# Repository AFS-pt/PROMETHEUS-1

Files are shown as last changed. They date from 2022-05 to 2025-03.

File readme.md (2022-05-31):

# PROMETHEUS - PocketQube Framework Designed for Research and Educational Access to Space

## Project Summary

The PROMETHEUS project aims at providing easy access to space for the research and education (R&E) community. Learning or researching about space can be more fruitful via hands-on projects. However, Space can seem like a pitfall environment with high risks and therefore high costs to develop projects at the student level. This barrier is critical and hinders R&E opportunities given the lack of experience in this environment. The team has identified that there is no current tool that enables easy and low-cost access to such space experiences of learning or manufacturing a simple satellite device. Looking into [Portugal’s Space 2030 national strategy](https://ptspace.pt/space-2030/), where we witnessed the creation of the [Portuguese Space Agency](https://ptspace.pt) and other related entities, the growing educational programs offered in Aerospace Engineering and the increasing interest of young students and researchers in this field, there is here an opportunity and a need to provide key tools to generate human critical mass.

The PROMETHEUS project aims at being a contributor for this momentum, by serving as an open-source PocketQube platform.

A PocketQube is a small satellite in a 5 cm cube form factor, an ideal size for R&E. The platform here proposed is based on the [PyCubed](https://github.com/pycubed) system (an open-source, radiation tested CubeSat avionics platform that integrates power, computing, communication, and attitude determination and control functionality into a single low-cost PC104-compatible module programmable entirely in Python), previously developed by the CMU team. This means that the entire system is widely available, based on commercial-off-the-shelf components and open-source hardware and software. From the foundation, the proposed platform has all the minimum required conditions to be easily integrated as a tool that facilitates hands-on activities and access to space.
But the PROMETHEUS goes beyond that and shares the entire pipeline for the satellite deployment as it will be licensed, certified, and launched. These steps are critical as, although there are a few design frameworks for PocketQubes available, there is a lack of information about the suitability of such designs to sustain the launch process. Moreover, from the licensing process, and considering that it needs to be performed through the competent national authorities, best-practice guidelines documentation is lacking among the community and if one intends to provide such a tool, it is important to share experiences and hurdles in this process.

**PROMETHEUS aims at giving access to space for everyone.**

## Expected Outputs

PROMETHEUS’s main objective is to provide a PocketQube platform that is tested and validated in space, and to make it openly available for everyone to replicate and customize. To accomplish such a goal, the following milestones/outputs need to be reached:

1. Tune the PyCubed platform for the ProcketQube form factor (PROMETHEUS blueprints).
2. Build the PROMETHEUS in different locations and by different people, based on the provided blueprints (replication validation).
3. License and certify the PROMETHEUS (authorization documentation).
4. Launch and validate
5. Share the knowledge (disseminate PROMETHEUS)

If all milestones are successfully accomplished, PROMETHEUS will be the first Portuguese PocketQube in space, as a result of a joint endeavour between Portuguese and CMU researchers, and hopefully will open the road for other national and international groups to do the same.

## Acknowledgment

The project "PROMETHEUS - PocketQube Framework Designed for Research and Educational Access to Space" (ref. CMU/TIC/0017/2021) is supported by [Portuguese Foundation for Science and Technology](https://www.fct.pt/index.phtml.en) under the International Partnership [CMU Portugal Program](https://www.cmuportugal.org), in a consortium between [Universidade do Minho](https://www.uminho.pt/EN/Pages/default.aspx) (PT), [Instituto Superior Técnico](https://tecnico.ulisboa.pt/en/) (PT) and [Carnegie Mellon University](https://www.cmu.edu) (USA).

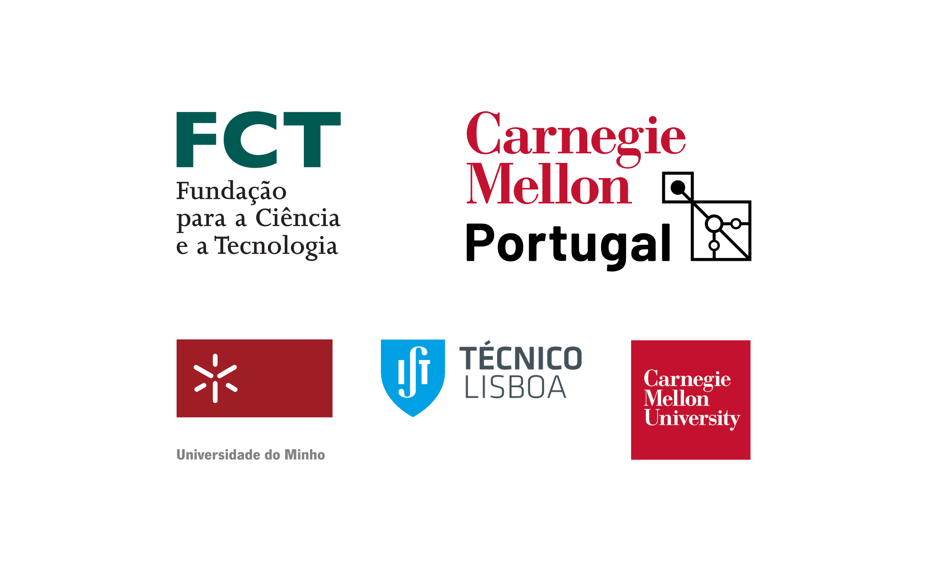
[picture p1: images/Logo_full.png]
My Image


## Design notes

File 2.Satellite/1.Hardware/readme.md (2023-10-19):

# Boards

2023-02-03 - forked from PyCubed-Mini

# Mechanical Structure

2023-02-03 - forked from PyCubed-Mini

3D-printed structural material: Windform XT2

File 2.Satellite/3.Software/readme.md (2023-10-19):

# Software Testing

## Description

The mainboard (red) has all the main components present in the satellite, such as the microcontroller (ATSAMD51J19A), LoRa chip (RFM98), as well as some power and data management. The Z- Board (blue) is one of the edges of the PocketQube, designed to interface four solarpanels and the antenna.

RExLab Team shared some useful [documentation](https://pocketqube.readthedocs.io/en/latest/index.html) about the uC software implementation and a detailed CAD model of the satellite. Nevertheless, their Github repos contain most of the important info and code (https://github.com/PyCubed-Mini: /fight_software, /avionics-..., /Tests).

The uC is programmed in CircuitPython, which can be coded using Mu Editor. The code that arrived inside the board is inside "Software on board" folder.

<p align="middle">
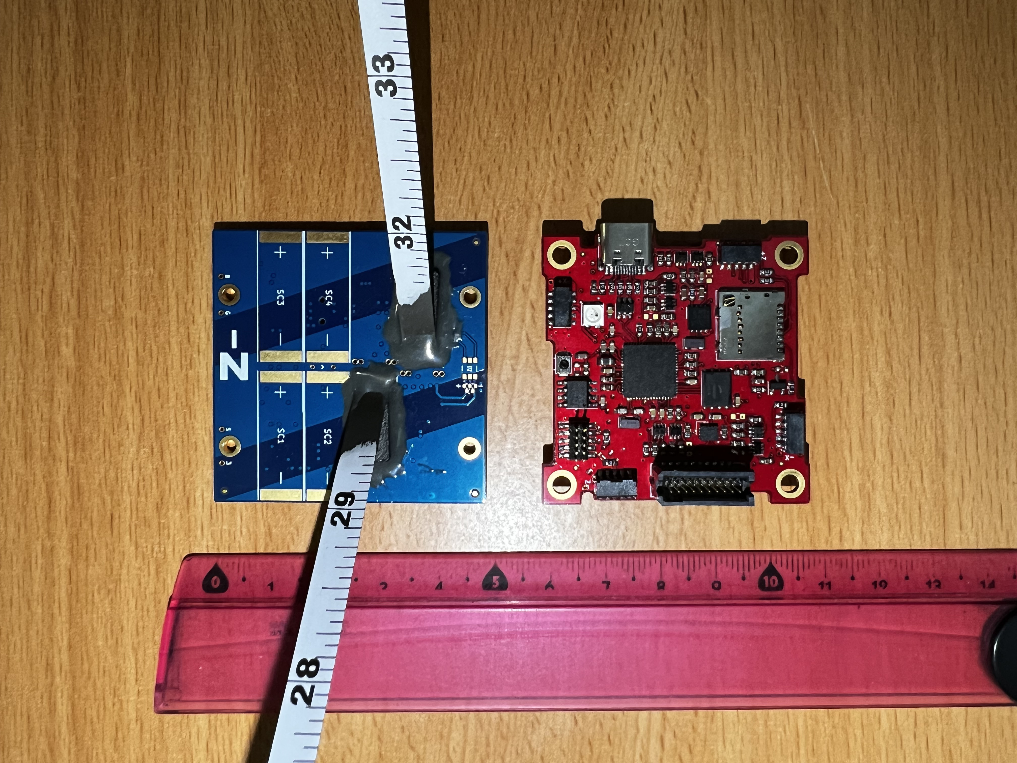
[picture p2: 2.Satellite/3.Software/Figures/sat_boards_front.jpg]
  
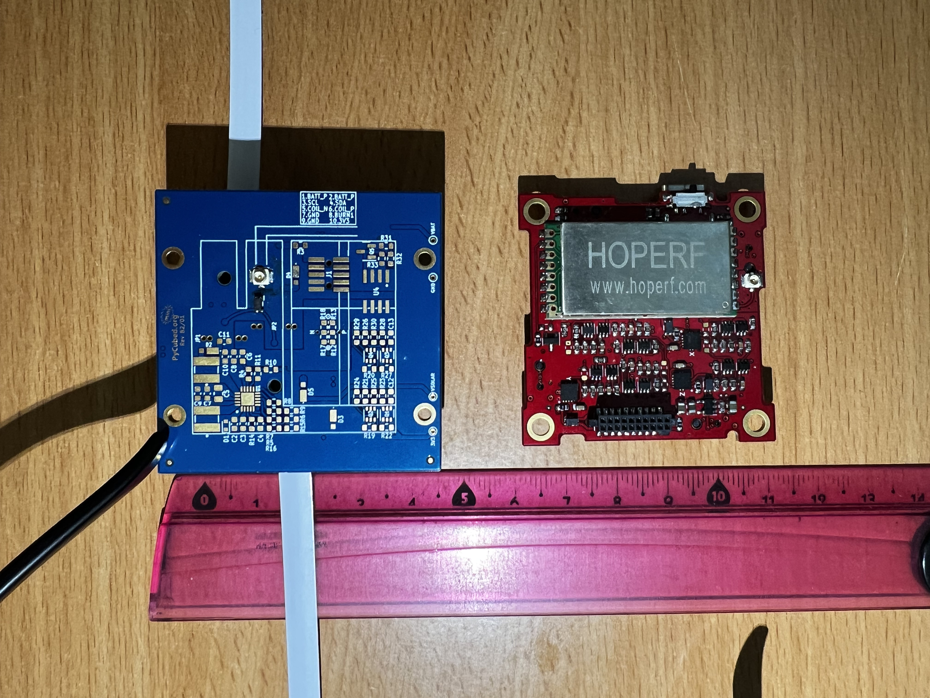
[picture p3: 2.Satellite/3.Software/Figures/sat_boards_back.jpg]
  
</p>

<br>

## First steps

1. Install Mu Editor from [Adafruit website](https://learn.adafruit.com/welcome-to-circuitpython/installing-mu-editor);

2. Connect an USB cable between your computer and the board;

3. Make sure that the switch below board USB-C port in turned on (right position);

4. Double-tap the button (there is only one);

5. If a USB unit isn't detected, there might be two issues:
    - Double-tap timing is wrong (keep trying);
	- USB-C connection (flip the USB-C cable at board connector);

6. Paste the code and libraries you want to run on the uC inside the USB unit;
    - See below the code used for testing LoRa packets transmission from satellite board to ground station [LILYGO® TTGO T-Beam v1.1](https://meshtastic.org/docs/hardware/devices/tbeam/);
    
7. In Mu Editor, open file from folder (main.py, for example) and open Serial Viewer;

8. Saving file edits should recompile the program, execute your code and show prints in serial data. If not, try Ctrl+D in Serial Viewer;

<br>

## Transmission from satellite board to ground station (LILYGO® TTGO T-Beam v1.1)

First, the steps needed for the ground station (receiver):

1. Install Arduino IDE;

2. Install the ESP32 board drivers (follow this [tutorial](https://randomnerdtutorials.com/installing-the-esp32-board-in-arduino-ide-windows-instructions/));
    - In our case, the board reference changes to 'TTGO LoRa32-OLED' and the COM port may be defined to another instance;

3. Install the libraries needed for peripherals, such as the OLED and LoRa chip (follow this [tutorial](https://randomnerdtutorials.com/ttgo-lora32-sx1276-arduino-ide/));

4. Create a project with the sender sketch from the last tutorial, compile, run and open Serial Viewer, configured with the correct parameters;
    - Again, in our case, change the board pins (MISO, SDA, ...) to the correct ones and frequency (433MHz);

5. The OLED should display the init prompt and starting to send packets;

Then, the steps needed for the mainboard (transmitter):

6. Download the Tests repo from PyCubed-Mini, more specifically the [LoRa Radio Range Test](https://github.com/PyCubed-Mini/Tests/tree/main/lora_radio_range_test) and do step 6 from last chapter;
    - This repo is really helpful since it has implemented easy and reliable testing routines to major components, such as the LoRa chip;
    - In our case, some modifications were necessary, such as the node address, receiving settings and string printing;

7. In the Seriel Viewer, it should prompt a interactive menu of the testing routine;

8. Select the satellite option, following the radio parameters change;
    - In our case, the default options were fine;

9. Finally, you should set the receiving mode with acknowledge;

10. In a few seconds, it should print the received LoRa packet info, such as the RSSI and the message;
    - As it is, the first four chars are not being printed as we hoped so;

<p align="middle">
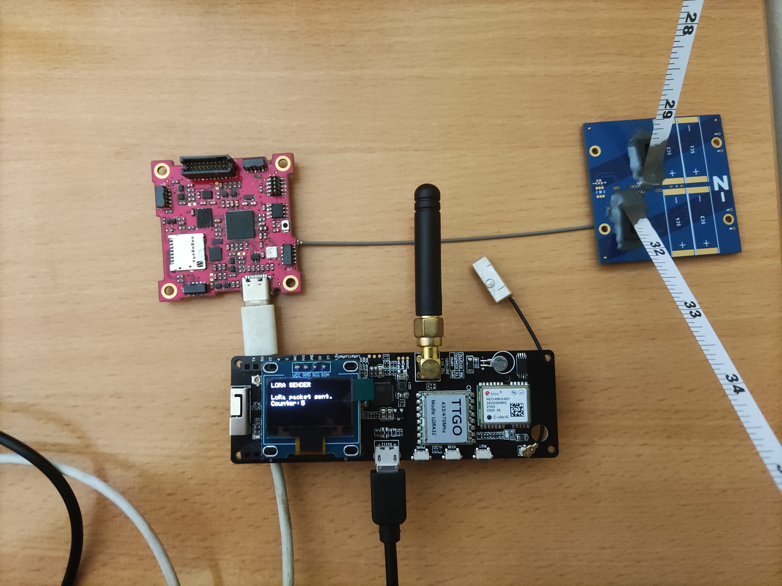
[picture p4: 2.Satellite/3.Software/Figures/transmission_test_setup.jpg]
  
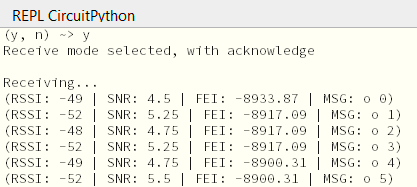
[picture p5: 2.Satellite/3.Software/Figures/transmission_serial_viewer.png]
  
</p>

<br>

## Transmission from ground station to satellite board

Not started but should be similar, since the satellite transmitting code could be functional in our case and the ground station receiving code could be like the one showed in the previous mentioned tutorial.

<br>

## Credits

We shared our files used, with our needed changes implemented, however we give all the credits to the rightful creators.

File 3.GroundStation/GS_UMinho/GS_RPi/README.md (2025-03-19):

# Raspberry Pi Ground Station

A small modular radio to chat with satellites.

## Features

- LoRa UHF communication (TX and RX);
- Compatible with Raspberry Pi (40-pin header);
- Programmed with CircuitPython;
- Independent power supply to increase performance;
- Dedicated to PROMETHEUS-1 satellite.

For more details on the RFM98 radio module, check the [short](https://www.hoperf.com/uploads/RFM98PW_RFM95PWRFTransmitterandReceiverModuleDatasheetREV1.1_1695351516.pdf) and [detailed](https://cdn.sparkfun.com/assets/learn_tutorials/8/0/4/RFM95_96_97_98W.pdf) datasheets.

## Hardware

### Issues

A few issues from RPiGS v2 were discovered during testing, which could be fixed in a new iteration (v2.1). These issues are detailed below:

1. [RESET pin of RFM9x radio should not have a pull-up resistor](https://github.com/adafruit/Adafruit_CircuitPython_RFM9x/pull/47):
    - v2: Resistor is present on both, but do not phisically assemble it.
    - v2.1: Resistor should be removed;

2. [Raspberry Pi pins CE0 and CE1 should not be used for GPIO purposes](https://learn.adafruit.com/circuitpython-on-raspberrypi-linux/spi-sensors-devices):
    - v2: CS pin is connected to CE0, but this line can be rearranged to another pin (such as D6) via software.
    - v2.1: RESET and CS pins from radio should be rerouted to other free GPIO pins;

3. Hat board power supply cannot power Raspberry Pi startup due to high initial current:
    - v2: radio and Raspberry can be powered by either Raspberry power module or by external power source.
    - v2.1: Raspberry should be only powered by its own power module, radio could be powered by either Raspberry power module or by external power source (probably increase transmission power).

## Software

### Instructions

#### Dependencies

Before using the RPiGS, make sure you have all the requirements, such as SPI enabled and CircuitPython installed. 

Based on [Adafruit tutorial](https://learn.adafruit.com/circuitpython-on-raspberrypi-linux/installing-circuitpython-on-raspberry-pi):

> Run these commands to enable the various interfaces such as I2C and SPI:
> ```bash
> user@machine ~
> $ sudo raspi-config nonint do_i2c 0
> $ sudo raspi-config nonint do_spi 0
> $ sudo raspi-config nonint do_serial_hw 0
> $ sudo raspi-config nonint do_ssh 0
> $ sudo raspi-config nonint do_camera 0
> $ sudo raspi-config nonint disable_raspi_config_at_boot 0
> ```
> 
> Then, install Blinka package and its dependencies with:
> ```bash
> user@machine ~
> $ sudo apt-get install -y i2c-tools libgpiod-dev python3-libgpiod
> $ sudo pip3 install --upgrade adafruit-blinka
> ```

Note that `--break-system-dependencies` might be needed. If it is undesirable please visit the original tutorial and install the package with a virtual environment.

> In Raspberry Pi model 5, RPi.GPIO is installed which causes issues. Just remove it with the following command:
> ```bash
> user@machine ~
> $ sudo pip3 uninstall -y RPi.GPIO
> ```
> 
> This script will automatically enable I2C and SPI. You can run the following command to verify:
> ```bash
> user@machine ~
> $ ls /dev/i2c* /dev/spi*
> ```
> 
> You should see the response:
> ```bash
> /dev/i2c-1 /dev/spidev0.0 /dev/spidev0.1
> ```

The following commands should also be executed if the hardware version is v2, as described in the issue #2 above.

> CE0 and CE1 can be reassigned via software with the commands:
> ```bash
> user@machine ~
> $ cd ~
> $ sudo pip3 install --upgrade adafruit-python-shell click
> $ wget https://raw.githubusercontent.com/adafruit/Raspberry-Pi-Installer-Scripts/main/raspi-spi-reassign.py
> $ sudo -E env PATH=$PATH python3 raspi-spi-reassign.py --ce0=5 --ce1=6
> ```
> 
> After this, the package should be properly installed. You can verify it with the following code:
> 
> ```python
> import board
> import digitalio
> import busio
> 
> print("Hello, blinka!")
> 
> # Try to create a Digital input
> pin = digitalio.DigitalInOut(board.D4)
> print("Digital IO ok!")
> 
> # Try to create an I2C device
> i2c = busio.I2C(board.SCL, board.SDA)
> print("I2C ok!")
> 
> # Try to create an SPI device
> spi = busio.SPI(board.SCLK, board.MOSI, board.MISO)
> print("SPI ok!")
> 
> print("done!")
> ```

#### Code

To run the ground station software, use the following command:
```bash
user@machine ~/PROMETHEUS-1/3.GroundStation/GS_UMinho/GS_RPi/Software/
$ python gs_shell.py
```

After this a prompt menu should appear, where you should select the option below to work with RPi_GS v2.
```bash
(o) RPiGS TX and RX (single radio)
```

Next, you can modify the radio parameters via prompt, but mind that these are the defined settings for PROMETHEUS-1. 

After this, you'll reach the ground station menu where you can request beacons, images, send commands, etc.

### References

Check the repositories from this was forked from:

- RPiGS single modem HW: https://github.com/cmu-spacecraft-design-build-fly-2023/Ops-Groundstation
- RPiGS dual modem HW: https://github.com/PyCubed-Mini/RPIGS/tree/main/rpi_dual_rfm98_hat
- RPiGS TX+RX LoRa/FSK SW: https://github.com/PyCubed-Mini/basic_groundstation/tree/image_radio_modes

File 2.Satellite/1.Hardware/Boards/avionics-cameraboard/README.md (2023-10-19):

avionics-cameraboard
Version B3/02
for updated versions, please consult https://github.com/PyCubed-Mini/avionics-cameraboard

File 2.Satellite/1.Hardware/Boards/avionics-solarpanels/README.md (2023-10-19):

# Solar Panels
PyCubedMini Solar Panel KiCAD projects.
Version B3/02
for updated versions, please consult https://github.com/PyCubed-Mini/avionics-solarpanels

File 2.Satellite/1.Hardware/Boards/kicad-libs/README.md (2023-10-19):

# kicad-libs
KiCad libraries for REx Lab avionics

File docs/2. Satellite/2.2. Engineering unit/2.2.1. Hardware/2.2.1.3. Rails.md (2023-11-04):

# Rails

Rails are the structural supports of the stack. There are two pieces in each stack, on the top and on the bottom, in which they hold inserts, sorted by the 3 axis. They provide the screwthreads needed for securing each external panels, as well as the upper and lower internal ones.

They are usually build from 3D-printed polylactic acid (PLA), since it is a cheap, simple and effective solution for granting the required rigidity for a testing unit.

Also made from PLA, two small brackets are needed for adjusting the antenna strips angle, holded in place with two M2 screws and nuts of nylon.

The 3D models of each rail and brackets are released in [Mechanical Structure](https://github.com/AFS-pt/PROMETHEUS-1/blob/main/2.Satellite/1.Hardware/Mechanical_Structure).

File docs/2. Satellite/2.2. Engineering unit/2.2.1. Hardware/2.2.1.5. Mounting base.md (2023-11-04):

# Mounting base

The mounting base is 3D-printed from PLA to provide a stable and safe piece to the satellite be placed on. Also it helps to place it on a flat surface and to hold it without pressing any components. The sliding required to insert the satellite facilitates the trigger of the switch mechanism stated previously.

The 3D model is released in [Fixtures](https://github.com/AFS-pt/PROMETHEUS-1/blob/main/2.Satellite/1.Hardware/Fixtures).

Mounted satellite

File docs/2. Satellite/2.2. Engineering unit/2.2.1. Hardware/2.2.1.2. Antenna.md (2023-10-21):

# Antenna

When simplicity and flexibility are two major parameters when designing an foldable antenna for this satellite, conductive tape measure comes in hand to develop a feasible solution.

<br />

## Antenna strips

As mentioned before, the satellite antenna, composed of two tape measure strips, is soldered to the defined Z- board pads. The metallic tape measure required for the process must be of approximately 1 cm in width, be almost planar and if possible, made of a easy-soldable material. The tape reference used for the assembly was DEXTER 8MM.

<br />

## Fishing line

The fishing line used for passing through the tape measure strip hole and the burn wire must be multithreaded, as each thread is smaller, they are melted easier when current passes through the burn wire. The line reference used for the assembly was CAPERLAM 4X 0.16 mm.

<br />

## Burn wire

The burn wire is made of nickel and chrome alloy of size AWG30.

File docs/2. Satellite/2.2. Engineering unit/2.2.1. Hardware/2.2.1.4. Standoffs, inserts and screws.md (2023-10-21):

# Standoffs, inserts and screws

There are three major types of mechanical parts required for the satellite, mentioned in the subtitle. They are recommended to be made of brass, since it has low density, or alluminum alternatively for the same reason.

<br /> 

## Standoffs

First, the standoffs separate each inside board with the adequate space between them. There were two sizes used: 6 mm and 4 mm in length, with eight M3 units needed for each size.

<br /> 

## Heat inserts

Then, the heat inserts, as referred before, provide the screwthreads needed for securing the external boards to the internal stack. There are needed 24 units in total: 4 units of M3, for attaching the -Y board to the stack; and 20 units of M2, for attaching X, +Y and Z boards.

<br /> 

## Screws

Finally, the screws fix the boards mentioned above, therefore, it is needed: 4 units of M3 (4 mm) for screwing -Y board to the -Y rail; 4 units of M3 (6 mm) screws for +Y rail to the stack; and 20 units of M2 (5 mm) screws for X, +Y and Z boards.

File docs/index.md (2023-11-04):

# Welcome to the PROMETHEUS-1 project wiki!

This website is composed of indexed pages which describe some important documentation about the satellite, such as its assembly. Please check the side bar for all available pages.

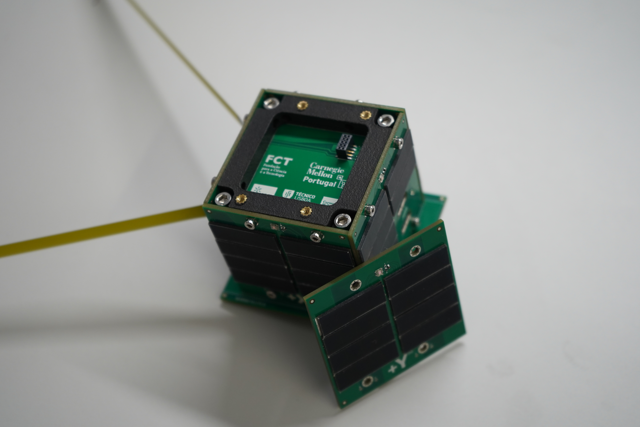
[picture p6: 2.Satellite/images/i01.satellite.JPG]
Satellite


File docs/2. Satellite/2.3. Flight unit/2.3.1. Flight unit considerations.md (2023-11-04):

# Flight unit considerations

This chapter explains only the different steps and precautions required during the flight unit manufacture, assembly and testing.

## Vibration testing and bake-out process

After the assembly, the satellite hardware must pass through vibration testing to certify that it can handle the launch. The vibration profile to test for is usually given by the launcher company and is specific for form factors or weight and the type of vibration. While all the tests are required for certification, usually the most important vibration test is the sinusoidal with frequencies up to 100 Hz, due to the predominance on launch. Consulting SpaceX Rideshare Payload User's Guide, the structure should handle at least 1.5 g. 

A vibe fixture was developed to couple the satellite with the vibration table, released on [Fixtures](https://github.com/AFS-pt/PROMETHEUS-1/blob/main/2.Satellite/1.Hardware/Fixtures). It is not recommended to use 3D-printed PLA as tends to damp higher frequencies and instead, consider alluminum for the case.

At last, the satellite goes through a bake-out process to accelerate outgassing, thus preventing contamination of the launcher pod and payload.

<br /> 

## Day in the life testing

Another important test is made to evaluate long-period satellite functioning. The test is performed by leaving the satellite running outdoors for an entire day, if possible being hit by the sun, to charge with the solar cells, and protected by the rain, to prevent damage. By the end of the test, the satellite should be running as it was left, and the batteries voltage be higher than previously.

<br /> 

## Assembly precautions

Before the procedure, drop and scrub the boards and its components with isopropyl alcohol (IPA). In this assembly procedure, more than required in engineering satellite units, the use of nitrile gloves and anti-static mat and wrist strap is very important. Although it is not mandatory, the assembly should be made in an ISO cleanliness certified room, if possible. Also, satellite transportation should be made inside an EMF protection bag, in a Nanuk case.

<br /> 

## Loctite usage

On flight unit, Loctite 222 is used in all screw surfaces. Just a few drops are enough to provide additional strength and prevent unscrewing.

<br /> 

## Windform rails

Instead of PLA rails, a carbon-fiber-reinforced polyamide material called [Windform XT 2.0](https://www.windform.com/sls-materials/windform-xt-2-0/) was used for the rails. It provides improved specific strength and NASA outgassing certification.

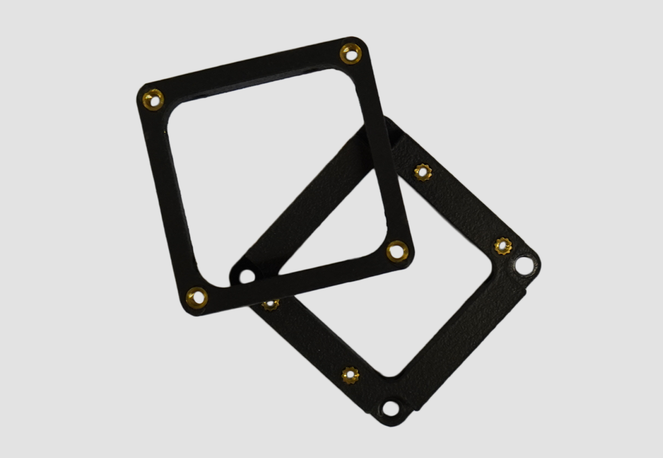
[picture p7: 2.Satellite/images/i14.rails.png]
Rails


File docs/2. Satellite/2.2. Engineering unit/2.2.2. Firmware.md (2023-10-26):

## Firmware

Preferably, you should skip building both the SAMD UF2 bootloader and CircuitPython files, as they are already released on [Firmware](/2.Satellite/Firmware), and skip to [Flashing SAMD UF2 bootloader](#flashing-samd-uf2-bootloader). However, some important references are given if you want to learn the required steps to build the [SAMD UF2 bootloader](https://github.com/PyCubed-Mini/uf2-samdx1) or [CircuitPython](https://github.com/PyCubed-Mini/circuitpython) yourself.

<br />

### Flash SAMD UF2 bootloader on mainboard

Based on [RExLab tutorial](https://github.com/PyCubed-Mini/avionics-mainboard/wiki/Flashing-UF2-Bootloader-on-the-ATSAMD51):

> The following procedure needs to be performed only once (barring any bricking / updating the bootloader) on a newly assembled mainboard with an unprogrammed MCU - in our case, the ATSAMD51J19A.
>
> <br /> 
>
> #### What you need
>
> - ATSAMD51 board (such as the PyCubed-Mini mainboard);
> 
> - Windows PC with atleast 2 free USB ports;
> 
> - SEGGER J-Link (we use the EDU Mini model);
> 
> - 2x5 pin 1.27mm pitch ribbon cable;
> 
> - USB-C and micro-USB cables, both with power and data lines;
>
> - SAMD bootloader binary file.
>
> <br /> 
>
> #### Step 1: Set up your PC
> 
> - Visit [Microchip Studio download page](https://www.microchip.com/en-us/tools-resources/develop/microchip-studio#Downloads), scroll down, and download the Web installer version of Microchip Studio. (The offline installer should also work, however I have had issues with antivirus software blocking it);
> 
> - Accept the Terms and Conditions, and deselect the "Send anonymous data" box. On the next page, select the architectures you'd like to install - we will only be using SAM boards. Finally, deselect "Advanced Software Framework and Example Projects" as these are not necessary. The rest of the installation should be fairly straightforward;
>
> - If asked to install the XC8 compiler, simply hit "OK" without installing - it is not necessary for this guide;
>
> - Microchip Studio should now be set up and open;
>
> - Next, visit [SEGGER J-Link download page](https://www.segger.com/downloads/jlink/), and download the latest Windows version of the J-Link software. The install process for this is fairly straightforward. The default settings should work fine;
>
> - A new SEGGER J-Link DLL Updater window will open asking to update Atmel Studio to the latest SEGGER software version. Make sure the check mark is selected and click "OK";
> 
> - Your computer is now ready for flashing the bootloader.

<br /> 

#### Step 2: Flash the bootloader

- Plug one end of the ribbon cable on 2x5 connector of the main board. Make sure pin 1 of the ribbon cable (red wire) is matching pin 1 of the board connector (longer silkscreen mark); 
  
- Plug the other end on the J-Link. Make sure pin 1 of the ribbon cable is matching pin 1 of the connector (white dot);

- Plug the J-Link on your PC with the micro-USB cable;

- Plug the the main board on your PC with the USB-C cable;

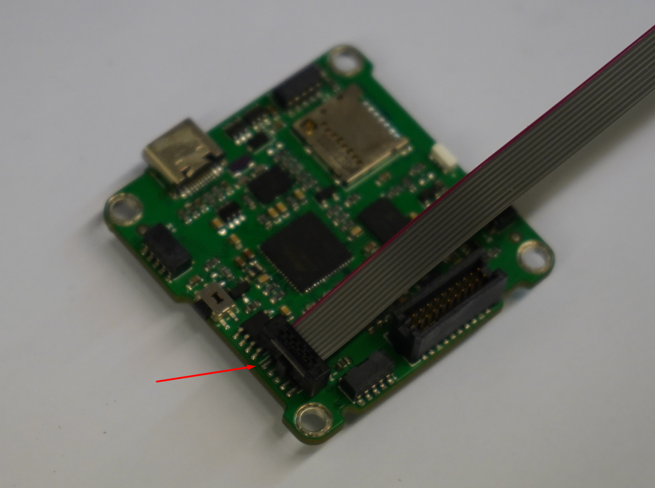
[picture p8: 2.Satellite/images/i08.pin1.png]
Pin 1


Based on [AdaFruit tutorial](https://learn.adafruit.com/how-to-program-samd-bootloaders/programming-the-bootloader-with-atmel-studio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):

> - Next, open Atmel Studio. From the toolbar, select "Tools" -> "Device Programming";
> 
> - The device programming window will open. Then, select "Tool" -> "J-Link";
>
> - If you're using a J-Link EDU, accept the terms of use that will pop up after selecting the J-Link interface;
>
> - After that, select the Device (the type of chip you're programming): ATSAMD51J19A and click "Read" in the top navigation bar. The empty fields for Device Signature and Target Voltage should populate;
> 
> *NOTE: Make sure these values appear before proceeding! If the board or your wiring is not detected, Atmel Studio will throw an error that it could not connect to the board. Check your wiring and try to connect again.*
>
> - On the sidebar, click Memories. On Flash, select the bootloader binary file that you either built or downloaded, and mark "Erase Flash before programming";
>
> - Click "Program", then "Verify";
>
> *NOTE: After clicking, the serial should output "OK" for each action, and there should be a new USB volume mounted on your machine.*

<br /> 

### Flash CircuitPython on mainboard

#### What you need

- PyCubed-Mini mainboard;

- PC with 1 free USB port;

- USB-C cable with power and data lines;

- CircuitPython UF2 file.

<br /> 

#### Step 1: Connect the board

- If you installed the bootloader right before, nothing should be made in this step;
  
- Otherwise, you should plug the board with the USB-C cable and the device should appear on your machine.

<br /> 

#### Step 2: Flash CircuitPython

Based on [AdaFruit tutorial](https://learn.adafruit.com/how-to-program-samd-bootloaders/installing-circuitpython):

> - Drag and drop the CircuitPython UF2 file that you either built or downloaded to the `pycubedminiBOOT` volume;
>
> - The volume should briefly disappear, and reappear as CIRCUITPY;
>
> - Your board is now running CircuitPython!

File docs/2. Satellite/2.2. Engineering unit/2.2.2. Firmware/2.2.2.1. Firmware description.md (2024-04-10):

# Firmware description

Preferably, you should skip building both the SAMD UF2 bootloader and CircuitPython files, as they are already released on [Firmware](https://github.com/AFS-pt/PROMETHEUS-1/blob/main/2.Satellite/2.Firmware), which were retrieved from [here](https://github.com/PyCubed-Mini/avionics-mainboard/tree/main/firmware/pycubedminiv03), and skip to [Flashing SAMD UF2 bootloader](https://afs-pt.github.io/PROMETHEUS-1/2.%20Satellite/2.2.%20Engineering%20unit/2.2.2.%20Firmware/2.2.2.2.%20Flash%20SAMD%20UF2%20bootloader%20on%20mainboard/). However, some important references are given if you want to learn the required steps to build the [SAMD UF2 bootloader](https://github.com/PyCubed-Mini/uf2-samdx1) or [CircuitPython](https://github.com/PyCubed-Mini/circuitpython) yourself.

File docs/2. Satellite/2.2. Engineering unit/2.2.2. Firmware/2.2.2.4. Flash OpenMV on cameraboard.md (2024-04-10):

# Flash OpenMV on cameraboard

## What you need

- PyCubed-Mini cameraboard;

- PC with 1 free USB port;

- USB-C cable with power and data lines;

- OpenMV IDE.

<br /> 

## Step 1: Connect the camera and plug the board

- After placing the camera on the board, connect it to your PC with the USB-C cable;

- Make sure the power switch on the board is turned on.

<br /> 

## Step 2: Flash OpenMV

- On OpenMV IDE, click on the bottom-left icon labeled as "Connect", as follow the GUI prompts;

*NOTE: There is a board switch connecting the BOOT0 pin to VDD, entering bootloader mode if asked in the GUI prompts.*

- Select "Yes" to confirm that the OpenMV camera (our cameraboard) is connected and paired;

- Select the correct board: OpenMV Cam H7 (STM32H743);

- Select "Yes" to erase internal file system;

- Unplug and plug again the USB-C cable;

- The GUI should automatically start deleting and programming the bootloader. When finished, a success message should appear;

<br /> 

## Step 3: Test the camera

- If asked to register the OpenMV camera, you can ignore pressing "No" to all prompts;

- If everything worked as planned, you should be back to the IDE code, with the `helloword.py` code file open. If that's not the case, you can open the file in IDE top-left, on `File > Examples > HelloWorld`;

- You can run this code by pressing the "Start" button on bottom-left and check the video feedback on the top-right.

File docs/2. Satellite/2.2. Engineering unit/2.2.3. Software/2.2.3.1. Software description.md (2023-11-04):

# Software description

After installing the firmware on the main and camera boards, some [Unitary testing](#unitary-testing) could be made to validate if everything is working as supposed, in an initial stage, or upload the code to run during launch and flight. To do so, some software applications must be built, in order to run files in our board(s). 

There are some already built and useful unitary testing scripts released in [Tests](https://github.com/AFS-pt/PROMETHEUS-1/blob/main/2.Satellite/3.Software/Tests), which will be mentioned in the next chapter. However, the Python software files for flight and system check are released in [Flight](https://github.com/AFS-pt/PROMETHEUS-1/blob/main/2.Satellite/3.Software/Flight), which require a build first, detailed right below. 

Based on [RExLab tutorial](https://pocketqube.readthedocs.io/en/latest/building.html):

> The frame folder contains the main.py (entry point for our software) and a custom state machine implementation.
>
> The drivers folder contains libaries allowing one to interface with the target hardware. We currently have the example emulator, pycubedmini driver and pycubedmini emulation.
>
> The applications folder contains the programs that utilize the drivers to achieve the specific mission objective. It contains the state machine configuration and tasks such as detumbling, beacon transmisions, logging and power management.

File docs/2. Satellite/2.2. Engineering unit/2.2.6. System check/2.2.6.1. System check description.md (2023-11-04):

# System check

This chapter describes the software application used for testing and validating the satellite's payload and core functioning. As it was expressed previously in chapter [Unitary testing: Mainboard payload](https://afs-pt.github.io/PROMETHEUS-1/2.%20Satellite/2.2.%20Engineering%20unit/2.2.4.%20Unitary%20testing/2.2.4.2.%20Mainboard%20payload/), the same code is used to now verify all eight tasks available. Also, if the unitary testing was performed, a detailed console log with its performance was noticeable, where some success criteria needed to be achieved in each trial to pass.

- SD card test: It displays if the SD card is detected or not;

- IMU test: Detects if IMU is functional and retrieve some accelerometer, gyroscope and magnetometer readings;

- Sun sensor test: Shows if all six sun sensors are functional and display some light intensity measurements;

- Coil driver test: Runs the drivers with three different voltage inputs, generating proportional magnetic fields with the driving current;

- Burn wire test: Applies a PWM signal (default duty-cycle is 0.3% for 3 secs) to the burn wire to validate the deploy mechanism;

- I2C test: Scans all integrated circuits and solar boards connected to the multiple I2C buses;

- NVM reset and test: Defaults the NVM counter and checks if its operation is right (requires the SD card);

- Current sensor test: Measures the current over a short period of time and looks for spikes or other anomalies that can translate in bad power supply;

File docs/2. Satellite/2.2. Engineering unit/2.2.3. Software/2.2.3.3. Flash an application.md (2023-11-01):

# Flash an application

This step is simple, as it only requires to drag the files and folders generated at the build directory and drop them inside satellite USB mounted volume.

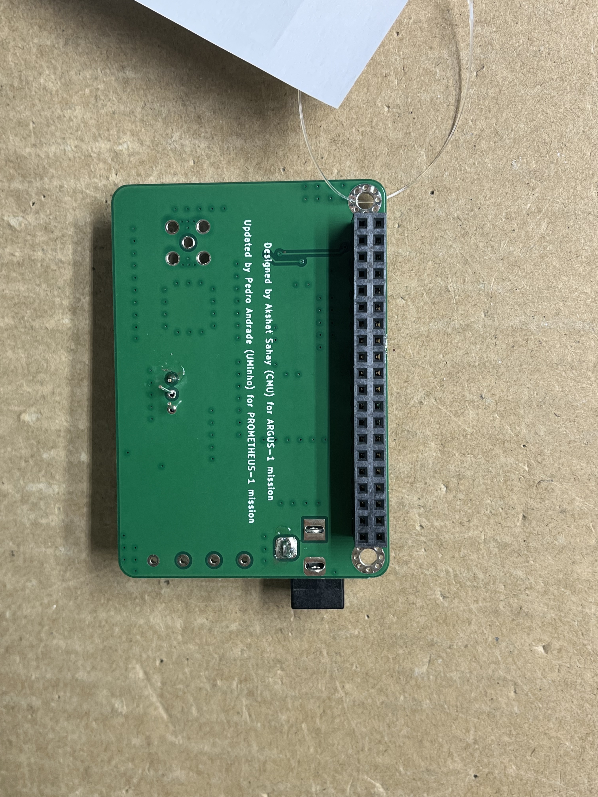
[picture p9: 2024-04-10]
3.GroundStation/GS_UMinho/GS_RPi/Hardware/PCBWAY/T-3FR54W488807A 2/081ffed555c88a33450b58737d8a0a5c.jpg

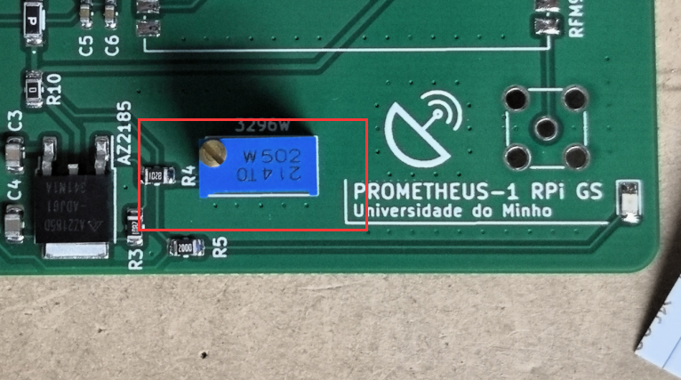
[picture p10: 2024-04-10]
3.GroundStation/GS_UMinho/GS_RPi/Hardware/PCBWAY/T-3FR54W488807A/Pls confirm the oreitation of resistors.png

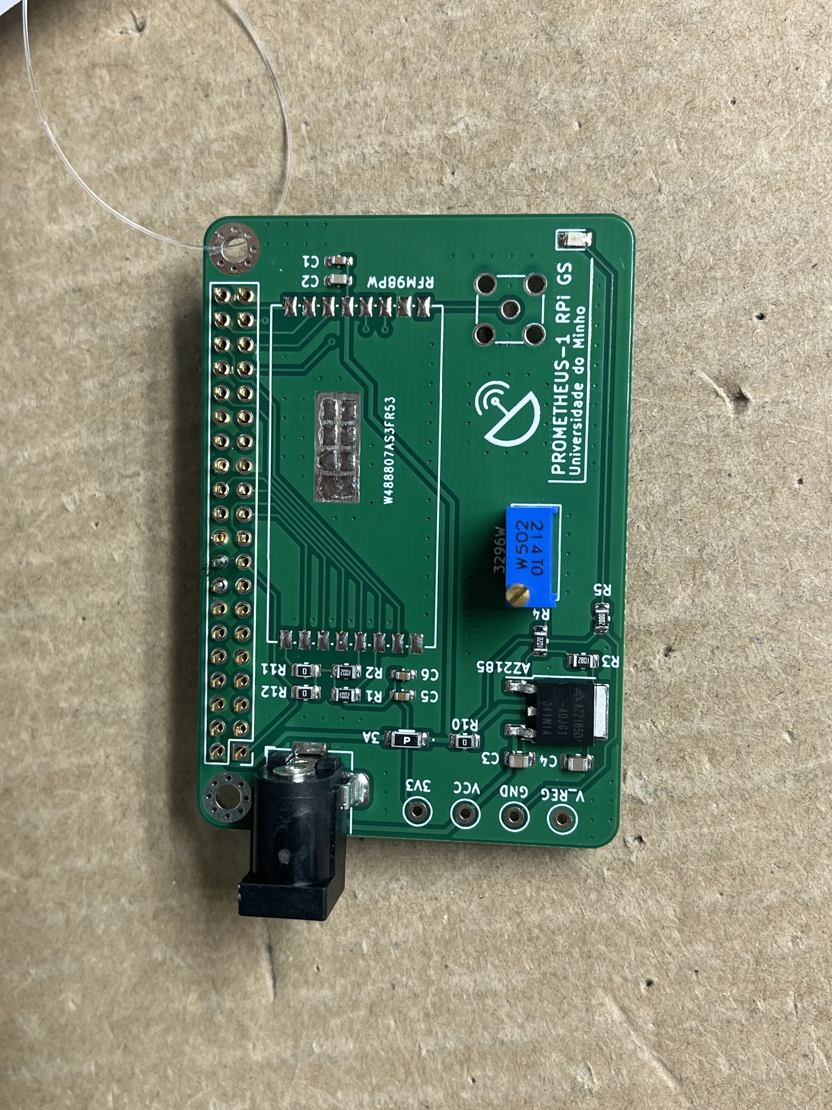
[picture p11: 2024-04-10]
3.GroundStation/GS_UMinho/GS_RPi/Hardware/PCBWAY/T-3FR54W488807A 2/e3172ede0ca46840ddab0fe581660beb.jpg

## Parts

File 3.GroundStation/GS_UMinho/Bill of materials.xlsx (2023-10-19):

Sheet: Lista componentes
Art. n.º | Descrição | Detalhes | Portes* | Preço ind. | Qt. | Preço parc.
Alimentação
1 | Pimenteiro (opt 1) (https://loja.watt.pt/material-electrico-quadros-electricos-quadro-de-obras-pimenteiro-c-6-tomadas-2p-t-shucko-c-disj.-s-cabo) | tudo-em-1 |  | €111.90 | 1 | €111.90
2 | Quadro (opt 2) (https://www.tecniled.pt/loja/quadros-eletricos-quadros-eletricos/distribuicao/superficie/q-din/quadro-q-din14-6-bases-16-32a-ip65/) | presume-se que só tem tomadas industriais (https://www.google.com/search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) | €0.00 | €100.74 | 1 | €100.74
3 | Quadro (opt 2) (https://www.tecniled.pt/loja/quadros-eletricos-quadros-eletricos/distribuicao/superficie/q-din/quadro-q-din20-8-bases-16-32a-ip65/) | 8 tomadas | €0.00 | €153.26 | 1 | €153.26
4 | Quadro (opt 3) (https://mauser.pt/catalog/product_info.php?cPath=1874_640_1964_3158&products_id=302-2942) | 6 tomadas |  | €89.90 | 1 | €89.90
5 | Adaptador quadro-tomada (opt 3 quadro) (https://mauser.pt/catalog/product_info.php?cPath=1874_640_1964_3158&products_id=302-3077) |  |  | €3.95 | 6 | €23.70
6 | Tomada PAWBOL (opt 1) (https://www.tme.eu/pt/details/pd.3146/conectores-de-rede-de-uma-so-fase/pawbol/d-3146/) | IP67, specs (http://www.pawbol.pl/en/nowosci/gz16ip67.htm) |  | €6.20 | 4 | €24.80
7 | Tomada PAWBOL S (opt 2) (https://www.tme.eu/pt/details/pd.3146s/conectores-de-rede-de-uma-so-fase/pawbol/d-3146s/) | IP67, terra compatível com fichas normais |  | €6.59 | 2 | €13.18
8 | Ficha PAWBOL (opt 1 tomada) (https://www.tme.eu/pt/details/pd.3148/conectores-de-rede-de-uma-so-fase/pawbol/d-3148/) | IP65 |  | €3.63 | 5 | €18.15
9 | Cabo elétrico XV (https://loja.watt.pt/cabo-xv-3g4-mm-4009) | 3G4mm2, 1m, para cabo geral |  | €2.10 | 10 | €21.00
10 | Cabo elétrico FVV (https://loja.watt.pt/material-electrico-cabos-cabo-fvv-cabo-fvv-3x2.5mm-h05vv-f-100mid=016-0637) | 3G2.5mm2, 1m, para instalação + chicotes |  | €1.44 | 10 | €14.40
11 | Bucim IP68 (https://mauser.pt/catalog/product_info.php?products_id=302-2790) | 5-10mm, para se cabo geral ligue direto ao disjuntor |  | €1.00 | 1 | €1.00
12 | Barramento Terra (https://mauser.pt/catalog/product_info.php?cPath=570_2336_3109_3111&products_id=302-2848) | 11 ligações |  | €4.56 | 1 | €4.56
13 | Barramento Neutro (https://mauser.pt/catalog/product_info.php?cPath=570_2336_3109_3111&products_id=302-2848) | 11 ligações |  | €4.56 | 1 | €4.56
14 | Interruptor diferencial LEGRANDE (https://www.tme.eu/pt/details/411017/disjuntores-diferenciais/legrand/p-312-c40-30-ac-dx/) | 2P, 40A, 30mA |  | €74.83 | 1 | €74.83
15 | Disjuntor HAGER (https://loja.watt.pt/material-electrico-disjuntores-diferenciais-aut.-escada-disjuntores-disjuntor-1p-16a-c-3ka-mw116-hager) | 1P, 16A |  | €1.96 | 6 | €11.76
Rede
16 | Raspberry Pi 4 (https://docs.google.com/spreadsheets/d/10-1Vyhc26uqYwxcJ5dKG7Qu3-UpelcF6-4yJfnXzVXE/htmlview) | NEEEICUM 2ª mão como novo | €0.00 | €90.00 | 1 | €90.00
17 | Sensor temperatura Raspberry (https://www.digikey.pt/pt/products/detail/adafruit-industries-llc/3721/8558266?productid=8558266) |  |  | €4.44 | 1 | €4.44
18 | Fonte alimentação Raspberry (https://mauser.pt/catalog/product_info.php?products_id=035-3401) |  |  | €8.70 | 1 | €8.70
19 | Cabo Ethernet (https://www.tme.eu/pt/details/u_utp6-cca-005yl/cabos-rj45/goobay/68433/) | 0.5m, CAT6, para interior |  | €0.86 | 2 | €1.72
20 | Cabo Ethernet (https://mauser.pt/catalog/product_info.php?cPath=1874_56_76_2728&products_id=015-0541) | rolo 100m, para exterior |  | €61.20 | 1 | €61.20
21 | Tomada RJ45/F-F (opt 1) (https://www.tme.eu/pt/details/log-np0083/conectores-rj/logilink/np0083/?brutto=1&currency=EUR) | IP68, CAT6a, sem bucim, para caixa |  | €9.38 | 4 | €37.52
22 | Tomada RJ45/F-F (opt 2) (https://www.tme.eu/pt/details/log-np0081/conectores-rj/logilink/np0081/?brutto=1&currency=EUR) | IP67, CAT6a, com bucim, para caixa |  | €9.09 | 4 | €36.36
23 | Ficha RJ45/M (https://mauser.pt/catalog/product_info.php?cPath=1874_640_358&products_id=011-3236) | blindada, FTP, CAT6a, para exterior |  | €0.81 | 1 | €0.81
24 | Tomada PAWBOL (https://www.tme.eu/pt/details/pd.3146/conectores-de-rede-de-uma-so-fase/pawbol/d-3146/) | IP67 |  | €6.20 | 1 | €6.20
25 | Barra de alimentação (https://www.tme.eu/pt/details/lps245/reguas-de-conexao/logilink/) | 4 tomadas (há versão com 3) |  | €5.48 | 1 | €5.48
26 | Caixa IP65 (https://www.tme.eu/pt/details/pw-s-box716/caixas-multifuncoes/pawbol/s-box-716/) | 300x380mm |  | €30.02 | 1 | €30.02
TinyGS
27 | Antena HYS OMNI (opt 1) (https://www.amazon.es/-/pt/gp/product/B08CC2CH5B/ref=ox_sc_saved_image_4?smid=A1693X2TF0DNMI&psc=1) | 3 dbi, 50W, 3m cabo, SMA/M | €0.91 | €54.99 | 1 | €55.90
28 | Antena EB-432/RK70CM (opt 2) [US] (https://www.m2inc.com/FGEB432RK70CM) | portes caros + problemas alfandegários | €299.99 | €321.99 | 1 | €621.98
29 | Antena EB-432/RK70cm (opt 2) [SWE] (https://www.antennerna.se/M2-EB-432-RK70cm) | sem stock + não entrega em Portugal | €73.00 | €493.41 | 1 | €566.41
30 | Antena EGB435RE (opt 3) (https://stecker-shop.net/epages/27edac8b-bca1-4619-a0d8-f53e62f2ef2c.sf/en_GB/) | 6.2 dbi, 100W, 0.5m, conector? | €14.06 | €233.06 | 1 | €247.12
31 | Antena OMB-433 (opt 4) (https://www.digikey.pt/en/products/detail/taoglas-limited/OMB-433-B06F21/6362795) | 6 dbi, 100W, 0.5m, N/F |  | €149.81 | 1 | €149.81
32 | LNA 440MHz Cubesat Filtered Preamp (opt 1) (https://store.uputronics.com/index.php?route=product/product&path=59&product_id=124) |  | €12.49 | €47.93 | 1 | €60.42
33 | LNA Amplifier 1-3000MHz (opt 2) (https://www.amazon.ae/gp/cart/view.html?ref_=nav_top_cart&language=en_AE&currency=EUR) | não entrega em Portugal | €0.00 | €10.53 | 1 | €10.53
34 | LNA4ALL (opt 3) (https://lna4all.blogspot.com/) |  | €7.00 | €20.00 | 1 | €27.00
35 | SMA DC Blocker (https://www.amazon.es/-/pt/dp/B07YYLHJKS) | <0.3dB |  | €24.04 | 1 | €24.04
37 | Fonte alimentação USB C (https://www.tme.eu/pt/details/posb05200a-usbc/fontes-de-alimentacao-de-contacto/pos/) |  |  | €5.04 | 1 | €5.04
38 | Fonte alimentação USB micro (https://www.tme.eu/pt/details/pos05100a-mu/fontes-de-alimentacao-de-contacto/pos/) |  |  | €3.97 | 1 | €3.97
39 | Conector N/M - SMA/M (opt 4 antena) (https://mauser.pt/catalog/product_info.php?cPath=1874_146_1041&products_id=011-3198) |  |  | €7.15 | 1 | €7.15
40 | Conector SMA/F-F (https://mauser.pt/catalog/product_info.php?cPath=1874_146_1849&products_id=011-3192) |  |  | €3.81 | 1 | €3.81
41 | Cabo SMA/M-M (https://www.tme.eu/pt/details/sma-m_m_50_0.2/cabos-de-ligacao-coaxial/mfg/sma-mm-50-0-2/) | 20cm, possui-se 1 un. |  | €5.46 | 1 | €5.46
42 | Tomada PAWBOL (https://www.tme.eu/pt/details/pd.3146/conectores-de-rede-de-uma-so-fase/pawbol/d-3146/) | IP67 |  | €6.20 | 1 | €6.20
43 | Barra de alimentação (https://www.tme.eu/pt/details/lps245/reguas-de-conexao/logilink/) | 4 tomadas (há versão com 3) |  | €5.48 | 1 | €5.48
44 | Caixa IP65 (https://www.tme.eu/pt/details/pw-s-box716/caixas-multifuncoes/pawbol/s-box-716/) | 300x380mm |  | €30.02 | 1 | €30.02

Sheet: Orçamento
Art. n.º | Descrição |  | Detalhes | Qt.
Alimentação
1 | Pimenteiro (opt 1) | https://loja.watt.pt/material-electrico-quadros-electricos-quadro-de-obras-pimenteiro-c-6-tomadas-2p-t-shucko-c-disj.-s-cabo | tudo-em-1 | 1
8 | Ficha PAWBOL (opt 1 tomada) | https://www.tme.eu/pt/details/pd.3148/conectores-de-rede-de-uma-so-fase/pawbol/d-3148/ | IP65 | 12 | comrpar de acordo com o pimenteiro
9 | Cabo elétrico XV |  | 3G4mm2, ROLO 100 METROS | 1
11 | Bucim IP68 | https://mauser.pt/catalog/product_info.php?products_id=302-2790 | 5-10mm, para se cabo geral ligue direto ao disjuntor | 1
Rede
16 | Raspberry Pi 4 - 8gb RAM | https://www.botnroll.com/pt/placas-controladoras-e-kits/3323-1618-raspberry-pi-4-model-b-15ghz.html |  | 1
17 | Sensor temperatura Raspberry | https://www.digikey.pt/pt/products/detail/adafruit-industries-llc/3721/8558266?productid=8558266 |  | 1
18 | Fonte alimentação Raspberry | https://www.botnroll.com/pt/fontes-de-alimentacao/3573-fonte-alimenta-o-oficial-raspberry-pi-4-usb-c-5-1v-3a-branco.html |  | 1
20 | Cabo Ethernet | https://mauser.pt/catalog/product_info.php?cPath=1874_56_76_2728&products_id=015-0541 | rolo 100m, para exterior | 1
21 | Tomada RJ45/F-F (opt 1) | https://www.tme.eu/pt/details/log-np0083/conectores-rj/logilink/np0083/?brutto=1&currency=EUR | IP68, CAT6a, sem bucim, para caixa | 4
22 | Bucim RJ45 |  | macho para apertar na opção anterior | 4
23 | Ficha RJ45/M | https://mauser.pt/catalog/product_info.php?cPath=1874_640_358&products_id=011-3236 | blindada, FTP, CAT6a, para exterior | 20
24 | Tomada PAWBOL | https://www.tme.eu/pt/details/pd.3146s/conectores-de-rede-de-uma-so-fase/pawbol/d-3146s/ | IP67 | 1
25 | Barra de alimentação | https://www.tme.eu/pt/details/lps245/reguas-de-conexao/logilink/ | 4 tomadas (há versão com 3) | 1
26 | Caixa IP65 | https://www.tme.eu/pt/details/pw-s-box716/caixas-multifuncoes/pawbol/s-box-716/ | 300x380mm | 1
TinyGS
27 | Antena HYS OMNI (opt 1) | https://www.amazon.es/-/pt/gp/product/B08CC2CH5B/ref=ox_sc_saved_image_4?smid=A1693X2TF0DNMI&psc=1 | 3 dbi, 50W, 3m cabo, SMA/M | 1
30 | Antena EGB435RE (opt 3) | https://stecker-shop.net/epages/27edac8b-bca1-4619-a0d8-f53e62f2ef2c.sf/en_GB/ | 6.2 dbi, 100W, 0.5m, conector? | 1
31 | Antena OMB-433 (opt 4) | https://www.digikey.pt/en/products/detail/taoglas-limited/OMB-433-B06F21/6362795 | 6 dbi, 100W, 0.5m, N/F | 1
 | MESHTASTIC ESP32 + LORA 433MHZ + GPS + DISPLAY + SUPORTE BATERIA 18650 | https://www.botnroll.com/pt/rf-lora/3973-esp32-lora-433mhz-gps-display-suporte-bateria-18650.html |  | 1
32 | LNA 440MHz Cubesat Filtered Preamp (opt 1) | https://www.kubii.fr/cartes-extension-cameras-raspberry-pi/3349-modules-amplificateurs-lna-avec-filtre-saw-3272496306646.html | Cubesat 435 MHz | 1
35 | SMA DC Blocker | https://www.amazon.es/-/pt/dp/B07YYLHJKS | <0.3dB | 1
37 | Fonte alimentação USB C | https://www.botnroll.com/pt/fontes-de-alimentacao/3573-fonte-alimenta-o-oficial-raspberry-pi-4-usb-c-5-1v-3a-branco.html |  | 1
38 | Fonte alimentação USB micro | https://www.tme.eu/pt/details/pos05100a-mu/fontes-de-alimentacao-de-contacto/pos/ |  | 1
39 | Conector N/M - SMA/M (opt 4 antena) | https://mauser.pt/catalog/product_info.php?cPath=1874_146_1041&products_id=011-3198 |  | 1
40 | Conector SMA/F-F | https://mauser.pt/catalog/product_info.php?cPath=1874_146_1849&products_id=011-3192 |  | 1
41 | Cabo SMA/M-M | https://www.tme.eu/pt/details/sma-m_m_50_0.2/cabos-de-ligacao-coaxial/mfg/sma-mm-50-0-2/ | 20cm, possui-se 1 un. | 1
42 | Tomada PAWBOL | https://www.tme.eu/pt/details/pd.3146s/conectores-de-rede-de-uma-so-fase/pawbol/d-3146s/ | IP67 | 1
43 | Barra de alimentação | https://www.tme.eu/pt/details/lps245/reguas-de-conexao/logilink/ | 4 tomadas (há versão com 3) | 1
44 | Caixa IP65 | https://www.tme.eu/pt/details/pw-s-box716/caixas-multifuncoes/pawbol/s-box-716/ | 300x380mm | 1

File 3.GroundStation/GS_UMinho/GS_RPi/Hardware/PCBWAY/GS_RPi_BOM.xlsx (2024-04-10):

Designator | Qty | Manufacturer | Mfg Part# | Descritption / Value | Value | Footprint
C1, C5, C6 | 3 |  |  | 0.1μF 0603 25V x7r | 0.1uF | Capacitor_SMD:C_0603_1608Metric_Pad1.08x0.95mm_HandSolder
C2 | 1 |  |  | 10μF 0603 25V x7r | 10uF | Capacitor_SMD:C_0603_1608Metric_Pad1.08x0.95mm_HandSolder
C3 | 1 |  |  | 10μF 0805 25V x7r | 10uF | Capacitor_SMD:C_0805_2012Metric_Pad1.18x1.45mm_HandSolder
C4 | 1 |  |  | 22μF 0805 25V x7r | 22uF | Capacitor_SMD:C_0805_2012Metric_Pad1.18x1.45mm_HandSolder
D1 | 1 | Broadcom Limited | HSMC-C170-T0000 | LED RED TOP MNT 2SMD | POW | LED_SMD:LED_0805_2012Metric_Pad1.15x1.40mm_HandSolder
ERBRG3R00V1 | 1 | Panasonic Electronic Components | ERB-RG3R00V | FUSE BOARD MOUNT 3A 32VDC 1206 | 3A | .MyLib:ERBRG4R00V
J1 | 1 | Samtec Inc. | SSW-120-02-G-D-LL | CONN RCPT 40POS 0.1 GOLD PCB | Raspberry_Pi_2_3 | Connector_PinSocket_2.54mm:PinSocket_2x20_P2.54mm_Vertical
J2 | 1 | Mueller Electric Co | BU-1420701211 | CONN SMA JACK STR. 50 OHM EDGE M | Coax SMA | Connector_Coaxial:SMA_Amphenol_901-144_Vertical
J3 | 1 | DC BARREL POWER JACK/CONNECTOR | PRT-00119 | SparkFun Electronics | Barrel_Jack | Connector_BarrelJack:BarrelJack_Horizontal
POT1 | 1 | Bourns Inc. | 3296W-1-502LF | TRIMMER 5K OHM 0.5W PC PIN TOP | 5K | Potentiometer_THT:Potentiometer_Bourns_3296W_Vertical
R1, R2 | 2 |  |  | 10K 0805 1% | 10K | Resistor_SMD:R_0805_2012Metric_Pad1.20x1.40mm_HandSolder
R3 | 1 |  |  | 2.8K 0805 1% | 2.8K | Resistor_SMD:R_0805_2012Metric_Pad1.20x1.40mm_HandSolder
R4 | 1 |  |  | 8.2K 0805 1% | 8.2K | Resistor_SMD:R_0805_2012Metric_Pad1.20x1.40mm_HandSolder
R5 | 1 |  |  | 200R 0805 1% | 200 | Resistor_SMD:R_0805_2012Metric_Pad1.20x1.40mm_HandSolder
R10-R12 | 3 |  |  | 0R 0805 1% | 0 | Resistor_SMD:R_0805_2012Metric_Pad1.20x1.40mm_HandSolder
U1 | 1 | HOPE MICROELECTRONICS | RFM98PW-433S2 | transceiver | RFM98PW | RF_Module_HOPERF:RFM95PW
U2 | 1 | Diodes Incorporated | AZ2185D-ADJTRG1 | IC REG LIN POS ADJ 4.95A TO252-3 | AZ2185D-ADJTRG1 | Package_TO_SOT_SMD:TO-252-2

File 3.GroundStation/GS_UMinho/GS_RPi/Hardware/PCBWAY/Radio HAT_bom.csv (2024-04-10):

Reference | Value | Footprint | Descritption | Manufacturer | Manufacturer ID | Qty
C1, C5, C6 | 0.1uF | Capacitor_SMD:C_0603_1608Metric_Pad1.08x0.95mm_HandSolder | 0.1μF 0603 25V x7r |  |  | 3
C2 | 10uF | Capacitor_SMD:C_0603_1608Metric_Pad1.08x0.95mm_HandSolder | 10μF 0603 25V x7r |  |  | 1
C3 | 10uF | Capacitor_SMD:C_0805_2012Metric_Pad1.18x1.45mm_HandSolder | 10μF 0805 25V x7r |  |  | 1
C4 | 22uF | Capacitor_SMD:C_0805_2012Metric_Pad1.18x1.45mm_HandSolder | 22μF 0805 25V x7r |  |  | 1
D1 | POW | LED_SMD:LED_0805_2012Metric_Pad1.15x1.40mm_HandSolder | LED RED TOP MNT 2SMD | Broadcom Limited | HSMC-C170-T0000 | 1
ERBRG3R00V1 | 3A | .MyLib:ERBRG4R00V | FUSE BOARD MOUNT 3A 32VDC 1206 | Panasonic Electronic Components | ERB-RG3R00V | 1
H1, H2 | M | MountingHole:MountingHole_2.7mm_M2.5_Pad_Via |  |  |  | 2
J1 | Raspberry_Pi_2_3 | Connector_PinSocket_2.54mm:PinSocket_2x20_P2.54mm_Vertical | CONN RCPT 40POS 0.1 GOLD PCB | Samtec Inc. | SSW-120-02-G-D-LL | 1
J2 | Coax SMA | Connector_Coaxial:SMA_Amphenol_901-144_Vertical | CONN SMA JACK STR. 50 OHM EDGE M | Mueller Electric Co | BU-1420701211 | 1
J3 | Barrel_Jack | Connector_BarrelJack:BarrelJack_Horizontal | SparkFun Electronics | DC BARREL POWER JACK/CONNECTOR | PRT-00119 | 1
J4 | VCC | TestPoint:TestPoint_Loop_D2.50mm_Drill1.0mm |  |  |  | 1
J5 | V_REG | TestPoint:TestPoint_Loop_D2.50mm_Drill1.0mm |  |  |  | 1
J6 | GND | TestPoint:TestPoint_Loop_D2.50mm_Drill1.0mm |  |  |  | 1
J7 | 3.3V | TestPoint:TestPoint_Loop_D2.50mm_Drill1.0mm |  |  |  | 1
POT1 | 5K | Potentiometer_THT:Potentiometer_Bourns_3296W_Vertical | TRIMMER 5K OHM 0.5W PC PIN TOP | Bourns Inc. | 3296W-1-502LF | 1
R1, R2 | 10K | Resistor_SMD:R_0805_2012Metric_Pad1.20x1.40mm_HandSolder | 10K 0805 1% |  |  | 2
R3 | 2.8K | Resistor_SMD:R_0805_2012Metric_Pad1.20x1.40mm_HandSolder | 2.8K 0805 1% |  |  | 1
R4 | 8.2K | Resistor_SMD:R_0805_2012Metric_Pad1.20x1.40mm_HandSolder | 8.2K 0805 1% |  |  | 1
R5 | 200 | Resistor_SMD:R_0805_2012Metric_Pad1.20x1.40mm_HandSolder | 200R 0805 1% |  |  | 1
R10-R12 | 0 | Resistor_SMD:R_0805_2012Metric_Pad1.20x1.40mm_HandSolder | 0R 0805 1% |  |  | 3
U1 | RFM98PW | RF_Module_HOPERF:RFM95PW | transceiver | HOPE MICROELECTRONICS | RFM98PW-433S2 | 1
U2 | AZ2185D-ADJTRG1 | Package_TO_SOT_SMD:TO-252-2 | IC REG LIN POS ADJ 4.95A TO252-3 | Diodes Incorporated | AZ2185D-ADJTRG1 | 1

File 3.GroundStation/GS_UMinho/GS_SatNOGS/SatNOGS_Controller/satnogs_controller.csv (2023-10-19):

Reference | Quantity | Value | Footprint | Datasheet | Mnf. | Price
A1 A2 | 2 | Pololu_Breakout_A4988 | Module:Pololu_Breakout-16_15.2x20.3mm | https://www.pololu.com/product/2980/pictures | - | -
C1 C11 C13 C2 C6 C7 | 6 | 0.1u | Capacitor_SMD:C_0805_2012Metric_Pad1.15x1.40mm_HandSolder |  | 08053C104KAT2A | 0.094
C10 | 1 | 10p | Capacitor_SMD:C_0805_2012Metric_Pad1.15x1.40mm_HandSolder |  | C0805C100K5GACTU | 0.091
C12 | 1 | 47u | Capacitor_SMD:C_1210_3225Metric_Pad1.42x2.65mm_HandSolder |  | GRM32ER61C476ME15L | 0.851
C14 C15 C3 | 3 | 100u | Capacitor_SMD:CP_Elec_6.3x5.3 |  | EXV107M016A9GAA | 0.443
C4 | 1 | 100u | Capacitor_THT:CP_Radial_D10.0mm_P5.00mm |  | RGA101M1JBK-1012G | 0.248
C5 | 1 | 2.2u | Capacitor_SMD:C_1210_3225Metric_Pad1.42x2.65mm_HandSolder |  | C3225X7R2A225K230AB | 0.697
C8 | 1 | 7.5n | Capacitor_SMD:C_0805_2012Metric_Pad1.15x1.40mm_HandSolder |  | GRM2195C1H752JA01D | 0.244
C9 | 1 | 100n | Capacitor_SMD:C_0805_2012Metric_Pad1.15x1.40mm_HandSolder |  | 08053C104KAT2A | 0.094
D1 | 1 | D_TVS | Diode_SMD:D_SMC_Handsoldering |  | SMCJ48CA-TR | 0.442
D2 D4 | 2 | D_Schottky | Diode_SMD:D_SMC_Handsoldering |  | CDBC560-G | 0.67
D3 | 1 | D_TVS_x2_AAC | Package_TO_SOT_SMD:SOT-23_Handsoldering |  | CDSOT23-SM712 | 1.53
F1 | 1 | FUSE | Fuse:Fuse_1206_3216Metric_Pad1.42x1.75mm_HandSolder |  | Littelfuse 1206SFS200F/63-2 | 0.6
FB1 | 1 | FILTER - POWER | Resistor_SMD:R_0805_2012Metric_Pad1.15x1.40mm_HandSolder |  | BLM21PG221SN1D | 0.104
FB2 | 1 | FILTER | Resistor_SMD:R_0805_2012Metric_Pad1.15x1.40mm_HandSolder |  | BLM21AG221SN1D | 0.141
JP1 JP2 JP3 JP4 JP5 JP6 JP7 JP8 | 8 | Jumper_NO_Small | Resistor_SMD:R_0805_2012Metric_Pad1.15x1.40mm_HandSolder |  | CRCW08050000Z0EA | 0.094
L1 | 1 | 27u | Inductor_SMD:L_Bourns_SRR1210A |  | SRR1210-270M | 1
P1 | 1 | ISP | Connector_PinHeader_2.54mm:PinHeader_2x03_P2.54mm_Vertical |  | - | -
P2 | 1 | INPUT | Connector_PinHeader_2.54mm:PinHeader_2x05_P2.54mm_Vertical |  | Amphenol-861400402YO2LF | 1.18
P3 | 1 | GND-PAD | MountingHole:MountingHole_2.2mm_M2_DIN965_Pad |  | - | -
P4 | 1 | I2C | Connector_PinHeader_2.54mm:PinHeader_2x04_P2.54mm_Vertical |  | - | -
P5 | 1 | End-Stops | Connector_PinHeader_2.54mm:PinHeader_2x03_P2.54mm_Vertical |  | - | -
P6 | 1 | DEV-PINS | Connector_PinHeader_2.54mm:PinHeader_2x04_P2.54mm_Vertical |  | - | -
P7 P8 | 2 | Motor | TerminalBlock_Phoenix:TerminalBlock_Phoenix_MKDS-1 | 5-4_1x04_P5.00mm_Horizontal |  | Amphenol-VI0421550000G | 0.84
R1 R2 | 2 | 10k | Resistor_SMD:R_0805_2012Metric_Pad1.15x1.40mm_HandSolder |  | CRCW080510K0JNEA | 0.091
R10 R14 | 2 | 200 | Resistor_SMD:R_0805_2012Metric_Pad1.15x1.40mm_HandSolder |  | CRCW0805200RJNEA | 0.091
R11 | 1 | 147k | Resistor_SMD:R_0805_2012Metric_Pad1.15x1.40mm_HandSolder |  | CRCW0805147KFKEA | 0.091
R12 | 1 | 10.5k | Resistor_SMD:R_0805_2012Metric_Pad1.15x1.40mm_HandSolder |  | CRCW080510K5FKEA | 0.091
R18 R19 | 2 | 100k | Resistor_SMD:R_0805_2012Metric_Pad1.15x1.40mm_HandSolder |  | CRCW0805100KJNEA | 0.091
R3 R4 | 2 | 10 | Resistor_SMD:R_0805_2012Metric_Pad1.15x1.40mm_HandSolder |  | CRCW080510R0JNEA | 0.091
R5 | 1 | 120 | Resistor_SMD:R_0805_2012Metric_Pad1.15x1.40mm_HandSolder |  | CRCW0805120RJNEA | 0.091
R6 | 1 | 221k | Resistor_SMD:R_0805_2012Metric_Pad1.15x1.40mm_HandSolder |  | CRCW0805221KFKEA | 0.091
R13 R15 R16 R17 R7 R8 | 6 | 4.7k | Resistor_SMD:R_0805_2012Metric_Pad1.15x1.40mm_HandSolder |  | CRCW08054K70JNEA | 0.091
R9 | 1 | 26.7k | Resistor_SMD:R_0805_2012Metric_Pad1.15x1.40mm_HandSolder |  | CRCW080526K7FKEA | 0.091
U1 | 1 | SN65HVD485EDR | Package_SO:SOIC-8_3.9x4.9mm_P1.27mm |  | SN65HVD485EDR | 1.74
U2 | 1 | Arduino_Pro_Mini_328 | lsf-kicad-lib:Arduino_Pro_Mini_328 | https://cdn.sparkfun.com/datasheets/Dev/Arduino/Boards/Arduino-Pro-Mini-v14.pdf | - | -
U3 | 1 | TPS54360DDA | Package_SO:Texas_HSOP-8-1EP_3.9x4.9mm_P1.27mm_ThermalVias |  | TPS54360DDAR | 4
U4 | 1 | TC74 | Package_TO_SOT_SMD:SOT-23-5_HandSoldering |  | TC74A05.0VCTTR | 0.886
U5 | 1 | PCA9540B | Package_SO:TSSOP-8_3x3mm_P0.65mm |  | PCA9540BDP 118 | 1.23
U6 | 1 | Pololu_Dual_MC33926 | lsf-kicad-lib:Pololu_Dual_MC33926 | https://www.pololu.com/product/1213 | - | -

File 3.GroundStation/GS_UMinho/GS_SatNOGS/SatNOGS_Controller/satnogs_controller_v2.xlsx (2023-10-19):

Reference | Quantity | Value | Footprint | Manufacturer Part Number
C1 C11 C13 C2 C6 C7 | 6 | 0.1u | Capacitor_SMD:C_0805_2012Metric_Pad1.15x1.40mm_HandSolder | 08053C104KAT2A
C10 | 1 | 10p | Capacitor_SMD:C_0805_2012Metric_Pad1.15x1.40mm_HandSolder | C0805C100K5GACTU
C12 | 1 | 47u | Capacitor_SMD:C_1210_3225Metric_Pad1.42x2.65mm_HandSolder | GRM32ER61C476ME15L
C14 C15 C3 | 3 | 100u | Capacitor_SMD:CP_Elec_6.3x5.3 | EXV107M016A9GAA
C4 | 1 | 100u | Capacitor_THT:CP_Radial_D10.0mm_P5.00mm | RGA101M1JBK-1012G
C5 | 1 | 2.2u | Capacitor_SMD:C_1210_3225Metric_Pad1.42x2.65mm_HandSolder | C3225X7R2A225K230AB
C8 | 1 | 7.5n | Capacitor_SMD:C_0805_2012Metric_Pad1.15x1.40mm_HandSolder | GRM2195C1H752JA01D
C9 | 1 | 100n | Capacitor_SMD:C_0805_2012Metric_Pad1.15x1.40mm_HandSolder | 08053C104KAT2A
D1 | 1 | D_TVS | Diode_SMD:D_SMC_Handsoldering | SMCJ48CA-TR
D2 D4 | 2 | D_Schottky | Diode_SMD:D_SMC_Handsoldering | CDBC560-G
D3 | 1 | D_TVS_x2_AAC | Package_TO_SOT_SMD:SOT-23_Handsoldering | CDSOT23-SM712
F1 | 1 | FUSE | Fuse:Fuse_1206_3216Metric_Pad1.42x1.75mm_HandSolder | MP005478
FB1 | 1 | FILTER - POWER | Resistor_SMD:R_0805_2012Metric_Pad1.15x1.40mm_HandSolder | BLM21PG221SN1D
FB2 | 1 | FILTER | Resistor_SMD:R_0805_2012Metric_Pad1.15x1.40mm_HandSolder | BLM21AG221SN1D
JP1 JP2 JP3 JP4 JP5 JP6 JP7 JP8 | 8 | Jumper_NO_Small | Resistor_SMD:R_0805_2012Metric_Pad1.15x1.40mm_HandSolder | CRCW08050000Z0EA
L1 | 1 | 27u | Inductor_SMD:L_Bourns_SRR1210A | SRR1210-270M
P1 | 1 | ISP | Connector_PinHeader_2.54mm:PinHeader_2x03_P2.54mm_Vertical | TSW-103-07-G-D
P2 | 1 | INPUT | Connector_PinHeader_2.54mm:PinHeader_2x05_P2.54mm_Vertical | TSW-105-07-G-D
P4 | 1 | I2C | Connector_PinHeader_2.54mm:PinHeader_2x04_P2.54mm_Vertical | TSW-104-07-G-D
P5 | 1 | End-Stops | Connector_PinHeader_2.54mm:PinHeader_2x03_P2.54mm_Vertical | TSW-103-07-G-D
P6 | 1 | DEV-PINS | Connector_PinHeader_2.54mm:PinHeader_2x04_P2.54mm_Vertical | TSW-104-07-G-D
P7 P8 | 2 | Motor | TerminalBlock_Phoenix:TerminalBlock_Phoenix_MKDS-1 | VI0421550000G
R1 R2 | 2 | 10k | Resistor_SMD:R_0805_2012Metric_Pad1.15x1.40mm_HandSolder | CRCW080510K0JNEA
R10 R14 | 2 | 200 | Resistor_SMD:R_0805_2012Metric_Pad1.15x1.40mm_HandSolder | CRCW0805200RJNEA
R11 | 1 | 147k | Resistor_SMD:R_0805_2012Metric_Pad1.15x1.40mm_HandSolder | CRCW0805147KFKEA
R12 | 1 | 10.5k | Resistor_SMD:R_0805_2012Metric_Pad1.15x1.40mm_HandSolder | CRCW080510K5FKEA
R18 R19 | 2 | 100k | Resistor_SMD:R_0805_2012Metric_Pad1.15x1.40mm_HandSolder | CRCW0805100KJNEA
R3 R4 | 2 | 10 | Resistor_SMD:R_0805_2012Metric_Pad1.15x1.40mm_HandSolder | CRCW080510R0JNEA
R5 | 1 | 120 | Resistor_SMD:R_0805_2012Metric_Pad1.15x1.40mm_HandSolder | CRCW0805120RJNEA
R6 | 1 | 221k | Resistor_SMD:R_0805_2012Metric_Pad1.15x1.40mm_HandSolder | CRCW0805221KFKEA
R13 R15 R16 R17 R7 R8 | 6 | 4.7k | Resistor_SMD:R_0805_2012Metric_Pad1.15x1.40mm_HandSolder | CRCW08054K70JNEA
R9 | 1 | 26.7k | Resistor_SMD:R_0805_2012Metric_Pad1.15x1.40mm_HandSolder | CRCW080526K7FKEA
U1 | 1 | SN65HVD485EDR | Package_SO:SOIC-8_3.9x4.9mm_P1.27mm | SN65HVD485EDR
U3 | 1 | TPS54360DDA | Package_SO:Texas_HSOP-8-1EP_3.9x4.9mm_P1.27mm_ThermalVias | TPS54360DDAR
U4 | 1 | TC74 | Package_TO_SOT_SMD:SOT-23-5_HandSoldering | TC74A0-5.0VCTTR
U5 | 1 | PCA9540B | Package_SO:TSSOP-8_3x3mm_P0.65mm | PCA9540BDP,118

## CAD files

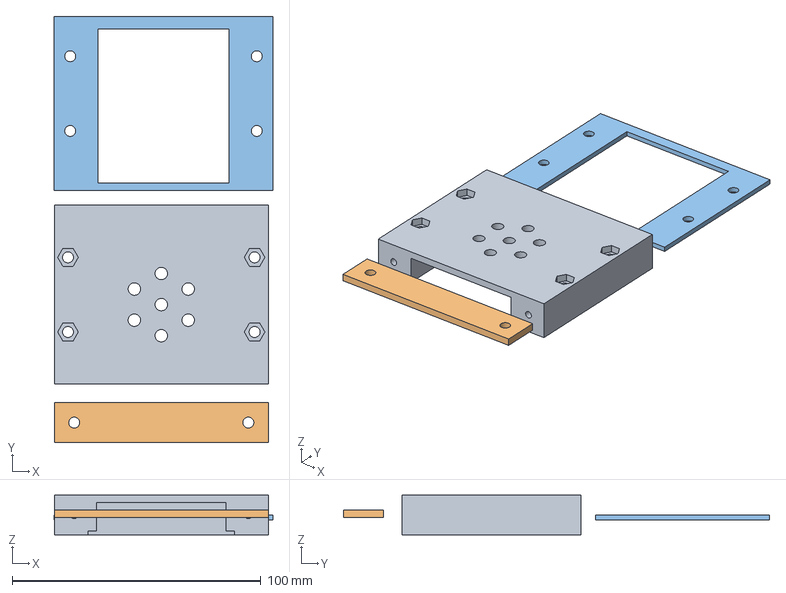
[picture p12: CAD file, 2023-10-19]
2.Satellite/1.Hardware/Fixtures/Vibe Plate Assembly v5.5.step
88.0 x 171.2 x 16.0 mm

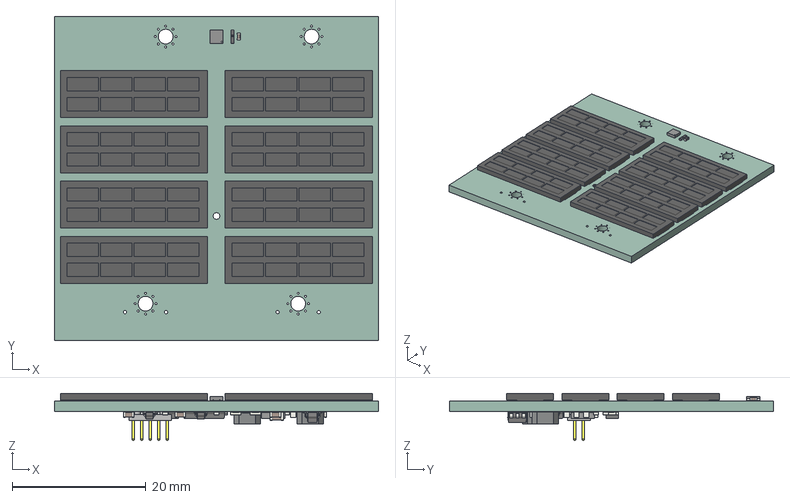
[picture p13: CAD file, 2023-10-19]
2.Satellite/1.Hardware/Boards/avionics-solarpanels/Solar-Panel-X+ (4L)/Solar-Panel-X+.step
48.4 x 48.4 x 7.09 mm
Solar-Panel-X PCB

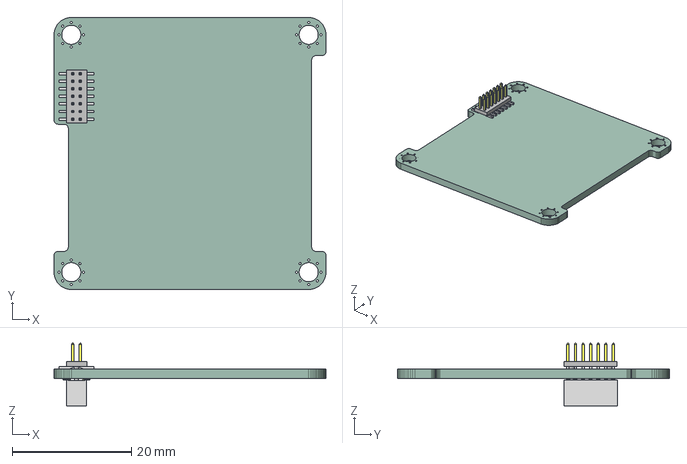
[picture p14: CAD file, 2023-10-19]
2.Satellite/1.Hardware/Boards/B3_03/avionics-batteryboard-main/batteryboard-middle/batteryboard-middle.step
45.6 x 45.6 x 10.5 mm
batteryboard-middle PCB

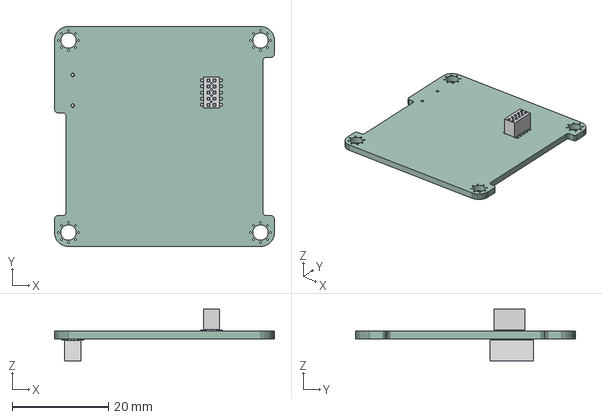
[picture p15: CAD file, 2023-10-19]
2.Satellite/1.Hardware/Boards/B3_03/avionics-batteryboard-main/batteryboard-top/batteryboard-top.step
45.6 x 45.6 x 10.8 mm
_autosave-batteryboard-top PCB

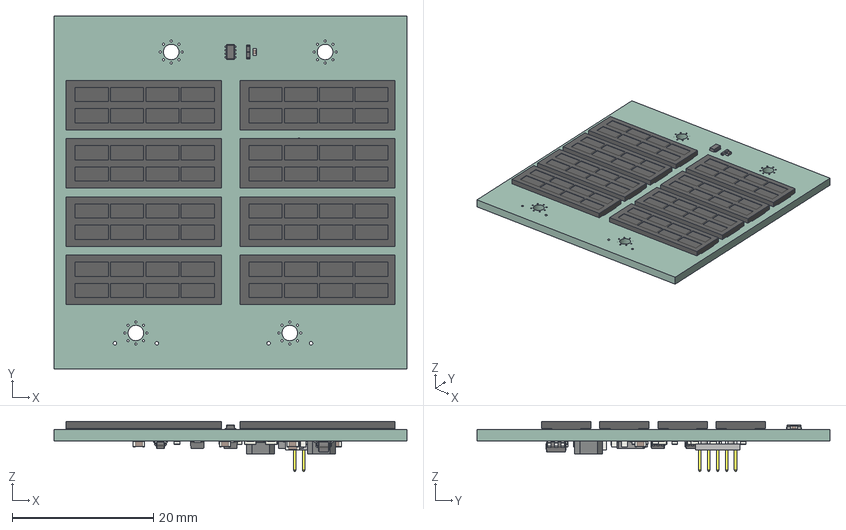
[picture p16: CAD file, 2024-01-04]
2.Satellite/1.Hardware/Boards/B3_03_next_version/avionics-solarpanels-main/Solar-Panel-Y+ (4L)/Solar-Panel-Y+.step
50.0 x 50.0 x 7.09 mm
Solar-Panel-Y+ PCB

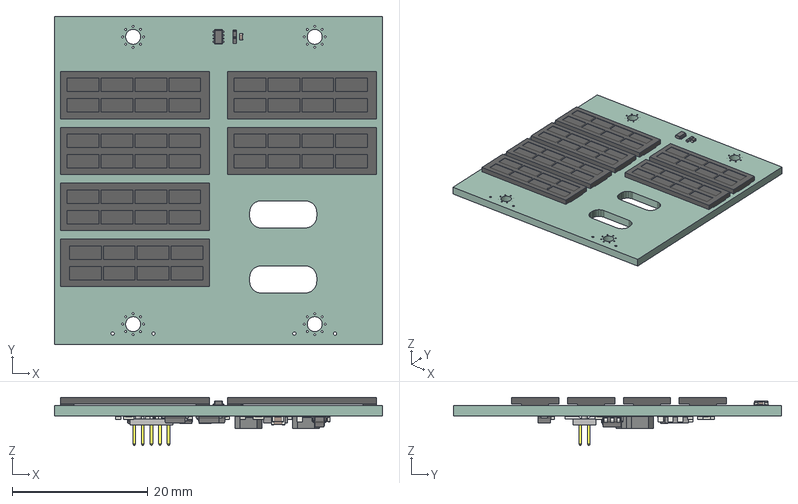
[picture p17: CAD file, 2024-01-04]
2.Satellite/1.Hardware/Boards/B3_03_next_version/avionics-solarpanels-main/Solar-Panel-Z+ (4L)/Solar-Panel-Z+.step
48.4 x 48.4 x 7.09 mm
Solar-Panel-Z+ PCB

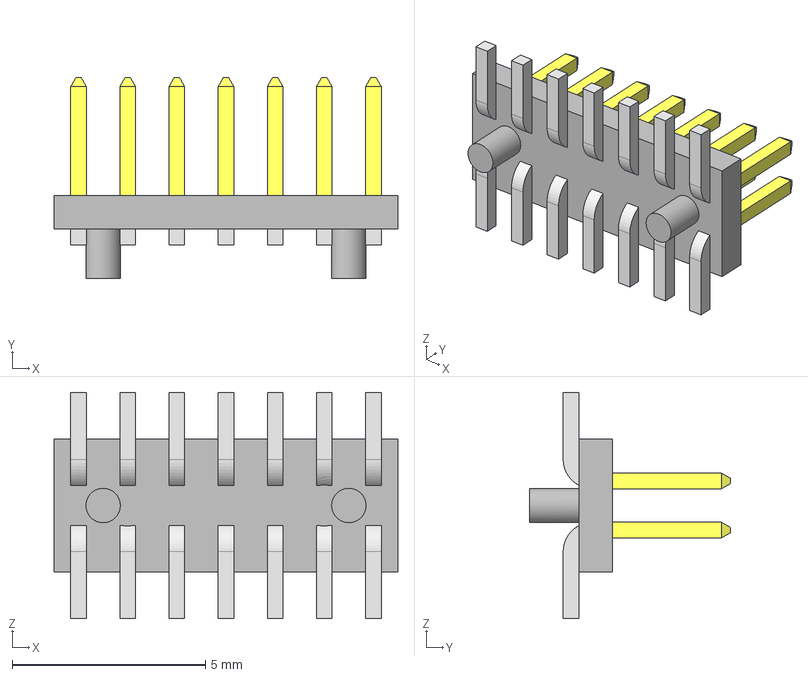
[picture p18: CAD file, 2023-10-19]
2.Satellite/1.Hardware/Boards/kicad-libs/3d/FTS-107-01-X-DV-A.stp
8.89 x 5.18 x 5.84 mm
FTS-107-01-L-DV-A_pins2
FTS-107-01-L-DV-A_pins1
FTS-107-01-L-DV-A_body

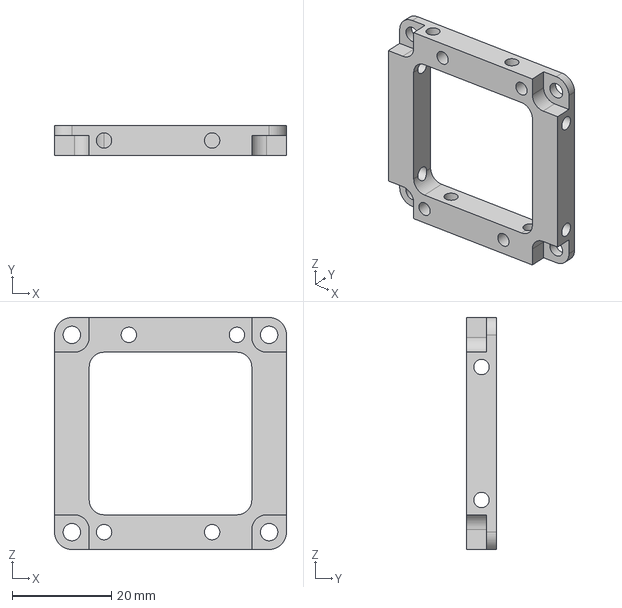
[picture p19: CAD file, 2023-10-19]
2.Satellite/1.Hardware/Mechanical_Structure/+Y Rail.step
46.8 x 6.00 x 46.8 mm

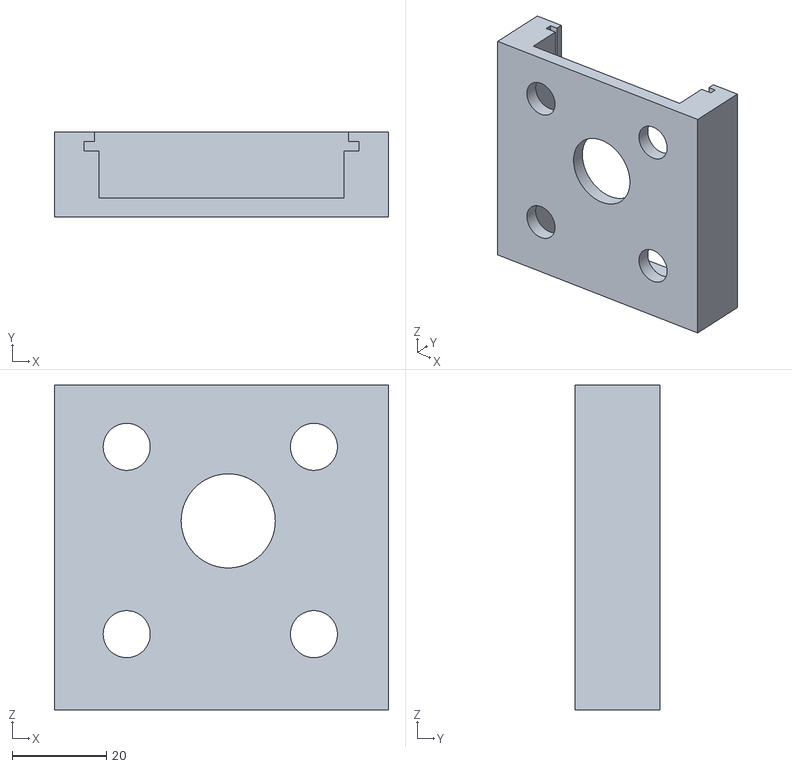
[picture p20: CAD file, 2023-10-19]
2.Satellite/1.Hardware/Fixtures/Mounting Base.stl
71.0 x 18.0 x 69.0

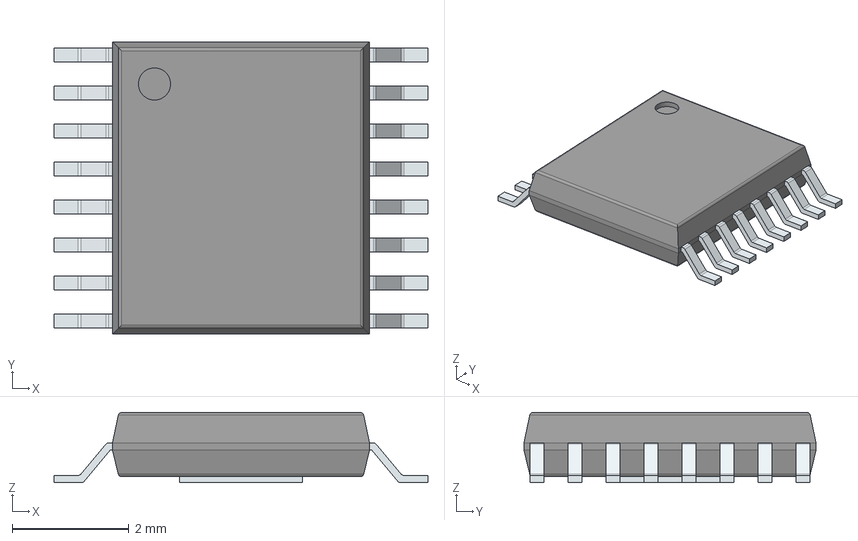
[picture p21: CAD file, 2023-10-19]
2.Satellite/1.Hardware/Boards/kicad-libs/3d/DRV8848PWPR.stp
6.40 x 5.00 x 1.20 mm
PinsArrayLR
ThermalPad

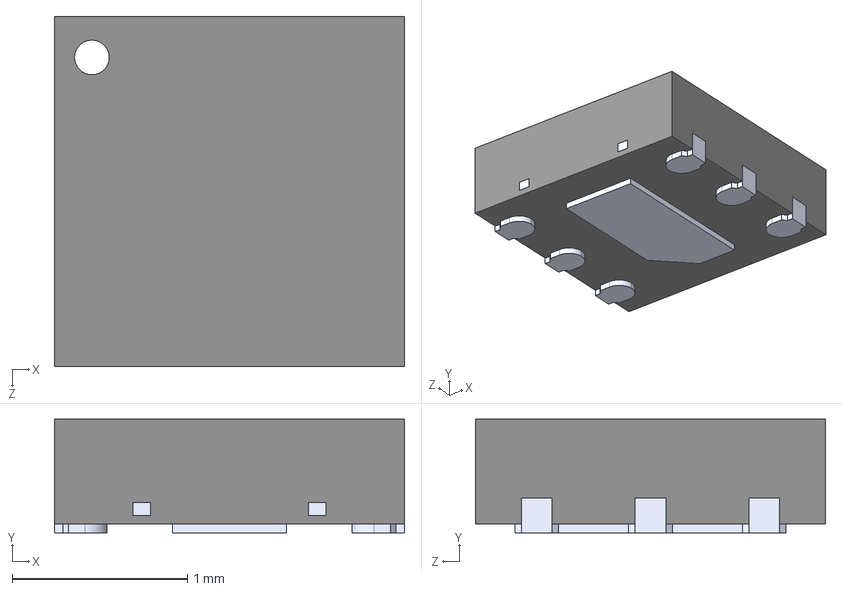
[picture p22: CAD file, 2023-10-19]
2.Satellite/1.Hardware/Boards/kicad-libs/3d/OPT3001.step
2.00 x 0.65 x 2.00 mm

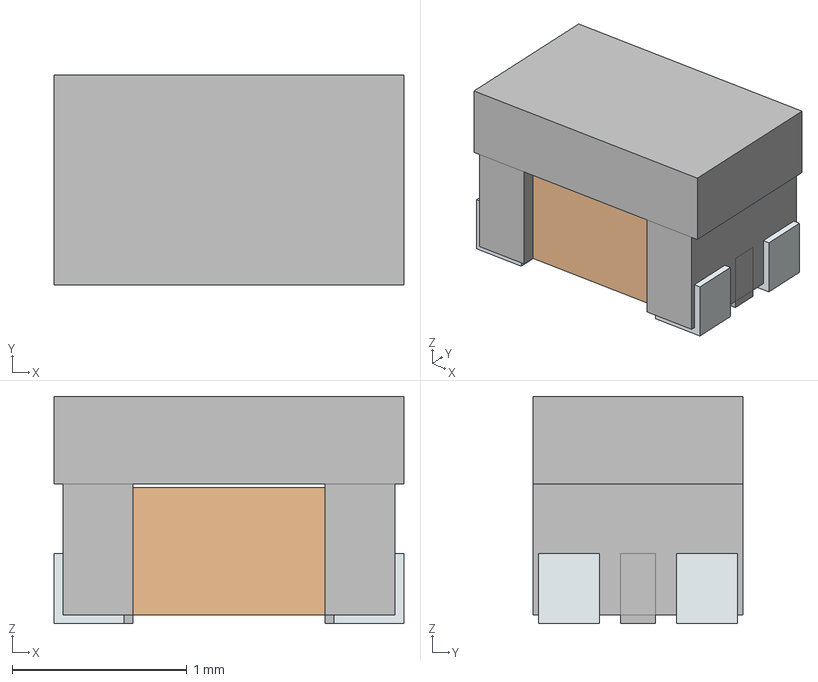
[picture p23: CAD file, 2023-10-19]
2.Satellite/1.Hardware/Boards/kicad-libs/3d/ATB2012-50011-T000.stp
2.00 x 1.20 x 1.30 mm
solidBody
solidLead
solidCoil

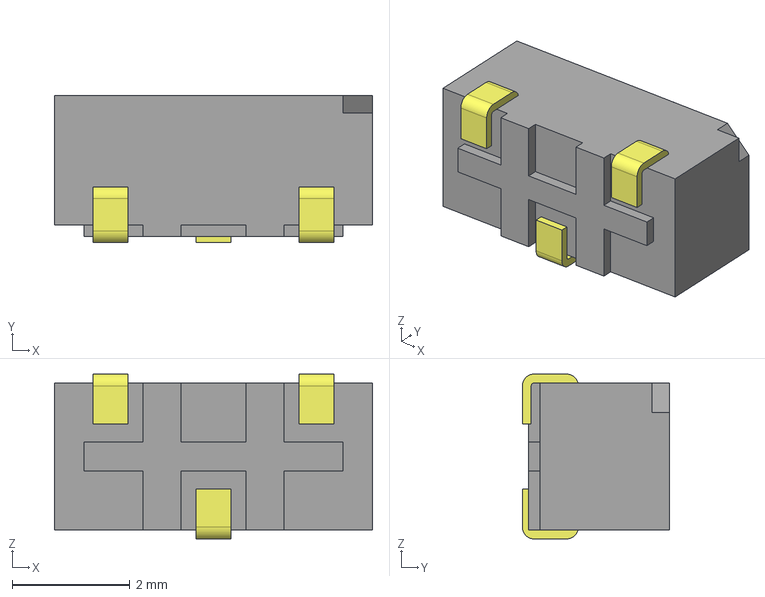
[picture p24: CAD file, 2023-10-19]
2.Satellite/1.Hardware/Boards/kicad-libs/3d/CAS-120TA.stp
5.40 x 2.50 x 2.80 mm
1 pole_s
CAS_c_12A

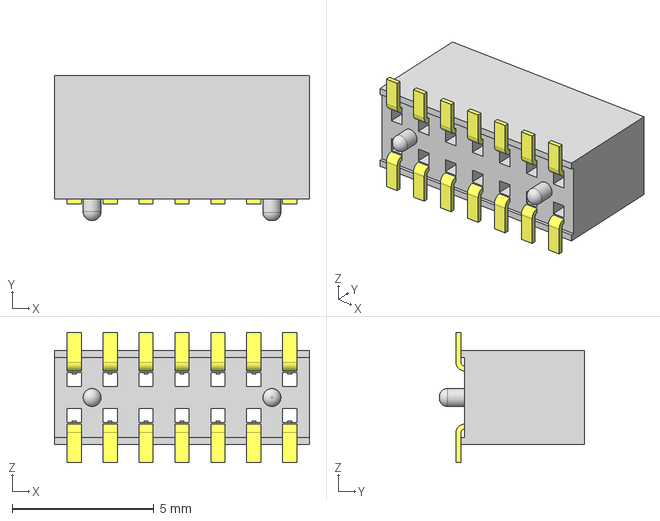
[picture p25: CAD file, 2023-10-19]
2.Satellite/1.Hardware/Boards/kicad-libs/3d/FLE-107-01-X-DV-A.stp
9.00 x 5.13 x 4.59 mm
C-96-01-07-DV
FLE-107-01-DV-A_socket

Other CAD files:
2.Satellite/1.Hardware/Boards/B3_03_next_version/avionics-solarpanels-main/Solar-Panel-X (4L)/Solar-Panel-X.step
2.Satellite/1.Hardware/Boards/kicad-libs/3d/BH1750FVI-TR.stp
2.Satellite/1.Hardware/Boards/kicad-libs/3d/Crystal_4pin_2520.STEP
2.Satellite/1.Hardware/Boards/avionics-solarpanels/Solar-Panel-Y+ (4L)/Solar-Panel-Y+.step
2.Satellite/1.Hardware/Boards/avionics-solarpanels/Solar-Panel-Z+ (4L)/Solar-Panel-Z+.step
2.Satellite/1.Hardware/Boards/kicad-libs/3d/1040310811.stp
2.Satellite/1.Hardware/Boards/kicad-libs/3d/150141M173100 (rev1).stp
2.Satellite/1.Hardware/Boards/kicad-libs/3d/434331045822.stp
2.Satellite/1.Hardware/Boards/kicad-libs/3d/5051102491.stp
2.Satellite/1.Hardware/Boards/kicad-libs/3d/B2B-PH-SM4-TB(LF)(SN).STEP
2.Satellite/1.Hardware/Boards/kicad-libs/3d/B3U-3000P.STEP
2.Satellite/1.Hardware/Boards/kicad-libs/3d/BH1750FVI.STEP
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

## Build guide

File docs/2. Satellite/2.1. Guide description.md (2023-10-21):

# Guide description

During two weeks on June 2023, a couple of stacks were successfully build at University of Minho, in which this guide is based. It provides a detailed step-by-step guide to correctly assemble and system check a PyCubed-Mini framework satellite of a PocketQube size. We also give some tips and useful notes for the process, learnt from this and previous builds at Carnergie Mellon University, where it was originally created and developed through multiple revisions.

During the development of a space mission, there are usually two separate units to build: an Engineering Unit and a Flight Unit. As the names sound, one is meant to validade all the hardware, firmware and software needed, while the other replicates it for a launch, ensuring extra safe and clean procedures, as required by launch companies.

This guide will be initially divided by each unit type, then mentioning the required parts to assemble each stack, describing the purpose and available options for fullfilling each one of the elements required. After, there will be some single testing of that parts, followed by the final assembly steps, for completing the stack, and final checking procedures.

This guide follows a sort of chronological order to facilitate its following, yet advised to fully read it first to avoid mistakes during the procedure.

Satellite

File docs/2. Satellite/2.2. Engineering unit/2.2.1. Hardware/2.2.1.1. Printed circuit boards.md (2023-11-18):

# Printed Circuit Boards (PCBs)

The PCBs are the fundamental hardware of the PyCubed-Mini, as they are precisely designed to hold its required components, as well as their connections, being that external, with USB-C connectors to easily interface with a computer or internal ones: between components in the same board, through the middle of it; or between board with stack connectors, with data and power lines.

The satellite is composed of eleven PCBs in total: five horizontally stacked inside, one on top of the other; and six covering each outside face of the cube. The KiCad schematics and board designs, as well as the gerber files for each are released in [Boards](https://github.com/AFS-pt/PROMETHEUS-1/blob/main/2.Satellite/1.Hardware/Boards). There are some components which require its schematic, footprint and CAD model to be imported to the KiCad project libraries to be fully recognized. To do so, please follow the [official KiCad documentation](https://docs.kicad.org/7.0/en/pcbnew/pcbnew_footprints_and_libraries.html#managing-footprint-libraries).

The recommended manufacturing option is to print the boards and solder the components at specialized companies, since there are multiple components in each board, some of them with different maximum temperature, in very reduced size or in need of a reflow oven.

This section will only mention the primary components and their references, discarding stack connectors and power regulation (present in all), reset and boot switches and status LEDs (present in some).

<br /> 

## Inside boards

The first group is divided in main board, camera board and battery boards.

<br /> 

### Main board

The main board contains the ATSAMD51J19A main microcontroller and MAX706 external watchdog timer, BNO085 IMU sensor and magnetorquer drivers, PCF8523 Real Time Clock, RFM98 radio module for 433 MHz LoRa communication, a USB-C connector for side power, flashing and communicating and SD Card connector for data logging.

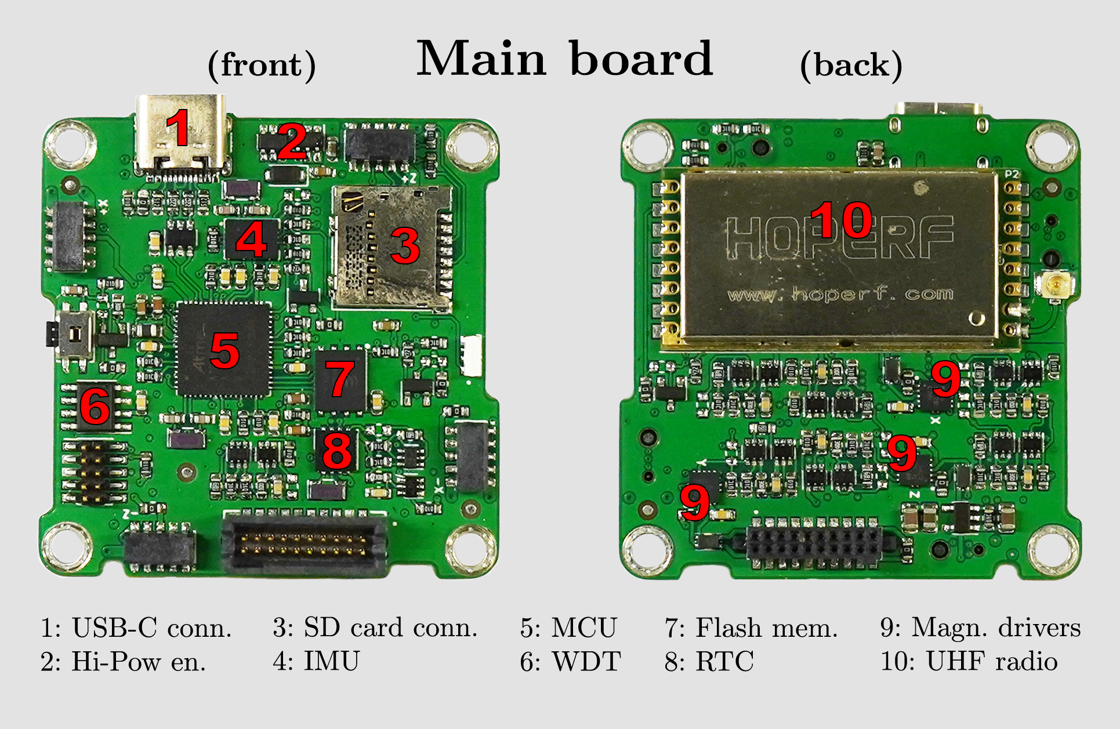
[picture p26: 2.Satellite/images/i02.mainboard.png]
Main board


<br /> 

### Camera board

The camera board, as the name tells, holds the OV5640 camera, the STM32H743VI camera microcontroller, an SD Card connector for image savings, and a USB-C connector, for the same reasons as the main board. The camera ribbon cable is placed on the desired connector and should be fixed in the center square with tiny quantities of epoxy.

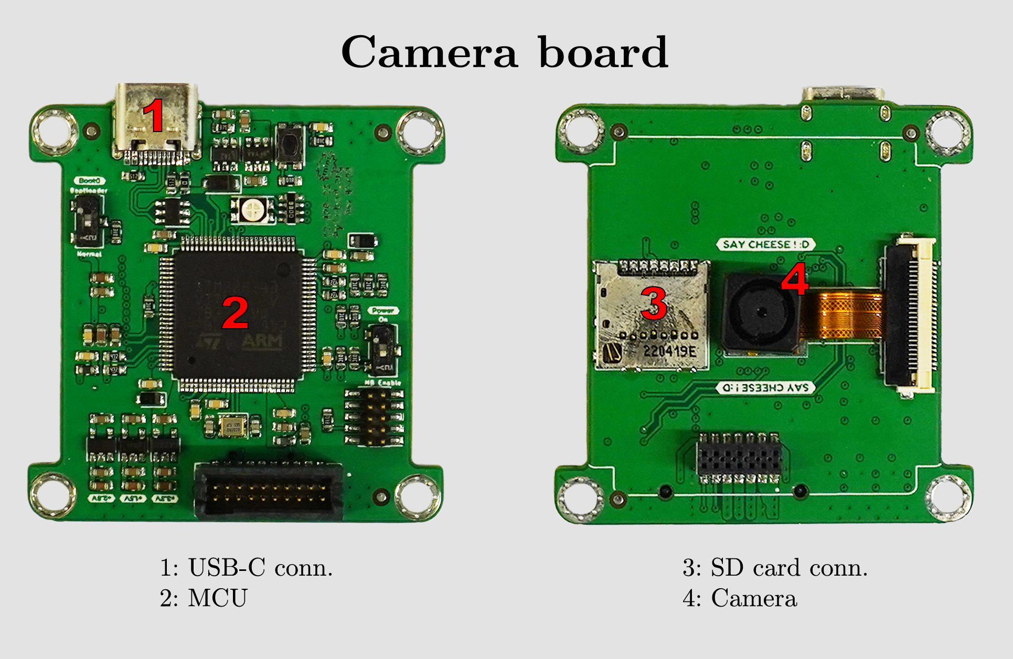
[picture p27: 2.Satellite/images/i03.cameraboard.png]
Camera board


<br /> 

### Battery boards

Two LP603443 batteries present in the satellite are placed between the three battery boards, wired in parallel for improved capacity, each with 3.7 V and 3.15 Wh. The circuitry is capable of sensing the current drawn and measuring its voltage.

Battery boards

<br /> 

## Outside boards

In all six solar boards (Figure 7), there are 14-turn coils serving as magnetorquers, 42 solar cells (KXOB25-05X3F) spread by the available space, energy harvesting systems, as well as OPT3001 sunlight sensors. There is also the antenna and burn wires, for its deployment, in one of the faces. Also, at the bottom one, there are two position switches that cut the battery power when pressed, preventing power draining during testing and storing. It has also a hole in the center, enabling the camera to take visible pictures.

Solar boards

In all solar boards, there is a 0 Ω resistor that is responsible for defining the correct I2C bus assignment. For negative axis boards, this SMD type wire pulls the I2C line to ground, while in positive boards, it should pull to power. 

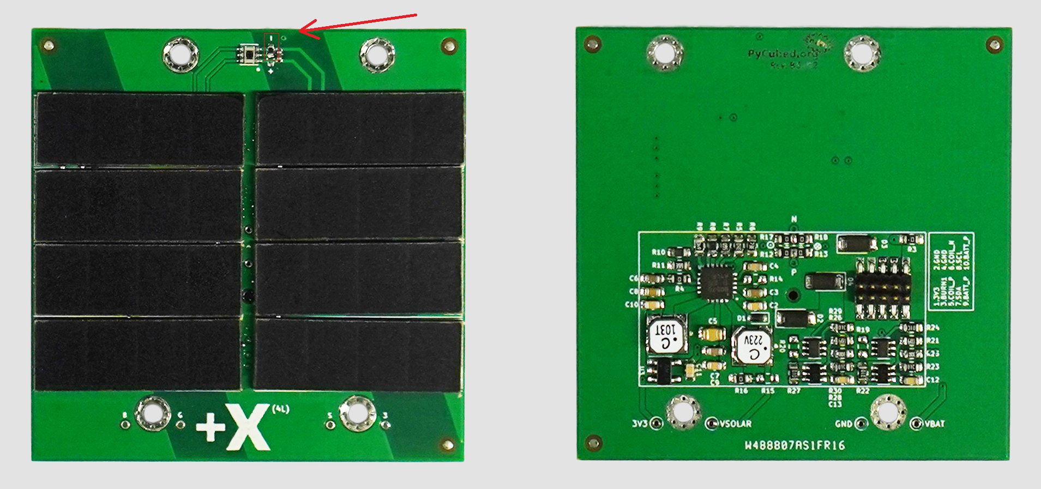
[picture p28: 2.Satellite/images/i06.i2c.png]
I2C


You can also check some important voltage potential values, such as (B)attery, (G)roud, (S)olar panels and (3).3 V, in the holes near the board edges.

<br /> 

### +X, -X, +Y boards

These boards are equal, composed of eight solar cells each. 

### -Y board

This board, besides the eight solar cells, holds two position switches that cut the battery power when pressed, preventing power draining during testing and storing. It has also a hole in the center, enabling the camera to take pictures.

### +Z board

This board holds the two holes needed for the USB-C connectors in main and camera boards, besides the six solar cells.

### -Z board

This board, besides the four solar cells, holds the antenna, which is holded in place with fishing line tied to each burn wire.

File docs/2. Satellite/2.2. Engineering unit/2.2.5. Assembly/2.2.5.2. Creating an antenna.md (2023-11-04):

# Creating an antenna

This chapter will describe how to create an antenna, detailing the tape strips, burnwire and brackets placement, along with the antenna tuning.

<br /> 

## What you need

- [Tape measure and burn wire](#antenna);

- [Brackets, nylon screws and nuts](#rails);

- 3M DP2216 epoxy or similar, with apply gun;

- Cardboard/PVC tube, with around 1 meter;

- Velcro tape with adhesive;

- u.FL male cable;

- Dremel tool;

- Soldering iron and solder;

- Cutting and drilling pliers;

- Sandpaper;

<br /> 

## Step 1: Prepare and place the tape

- Grab the referenced tape measure, get it out of the rolling box and cut at least two strips of around 20 cm each, making sure they are the same size;

- With a Dremel tool, remove around 3 cm from one of the sides of each strip to create an electrically conductive and solderable region;

*TIP: be extremely precise in removing all the paint around the edge to improve solderability.*

- At the recently scraped region, from about 1 cm of the tip, bend the strip 90 degrees to form a crease;

- Solder the creased tips of two strips to the antenna pads on the -Z board.

*NOTE: the soldering step must happen right after the scraping and bending due to oxidation issues on the strip.*

<br /> 

## Step 2: Prepare and place the burn wire

- Cut at least two burn wire pieces of aroung 3 cm each;

- Pass them through the specified holes, keeping the center of the wire, and the majority of its length, on the same side of the antenna strips;

- On the other side, bent the necessary to keep it in place, solder both contact points and cut the excedent wire.

<br /> 

## Step 3: Attach the antenna brackets

- After printing the brackets, place each between the antenna and the board, with the inclination touching the strip and its openings matching the board holes;

- Place a M2 nylon screw from the top through the bracket opening and the board hole, securing it with a corresponding nylon nut on the bottom side;

<br /> 

## Step 4: Tune the antenna

- Grab a 1 m cardboard/PVC tube and place the antenna board on one end and the VNA on the other, with velcro tape with adhesive, and connect the two (an adapter from u.FL to SMA connectors may be needed);

*NOTE: the tube creates a safe distance between the parts, in terms of eletromagnetic interference*

- With the VNA, measure the initial frequency, resistance and reactance of the antenna. The desired values are around 433 MHz, 50 Ω and 0 Ω, respectively.

- Disconnect the antenna from the VNA;

- For tuning the frequency, since it has an initial value below the desired, cut around 5 mm in each strip;

- Connect the antenna again and check the frequency;

*TIP: each 5 mm cut should decrease in aroung 10 MHz, however it is still recommended to cut that size at a time and remeasure*

- Repeat the last three points until the value is close to the desired, then reducing the cutting size to only 1 mm (or less);

- For tuning the reactance, adjust the position of the brackets by sliding them. Overall, widing the antenna will increase its reactance, narrowing will decrease it;

<br /> 

## Step 5: Final procedures

- Make sure you achieved the desired antenna parameters before proceeding;

- Make a 1 mm in diameter hole on the center of the outter edge (about 3 mm from the tip) of the antenna strips with a hole punch pliers, and sand it;

- Apply a good amount of epoxy on the sides of the brackets to fix it in position. Make sure the epoxy does not escape the board surface, neither touches the antenna strip or the nylon screw;

- Leave the board in a safe place to dry for about a day, and later remove the nylon pieces.

<br /> 

## Video guide

Press on the image to be redirected to view the video guide on YouTube.

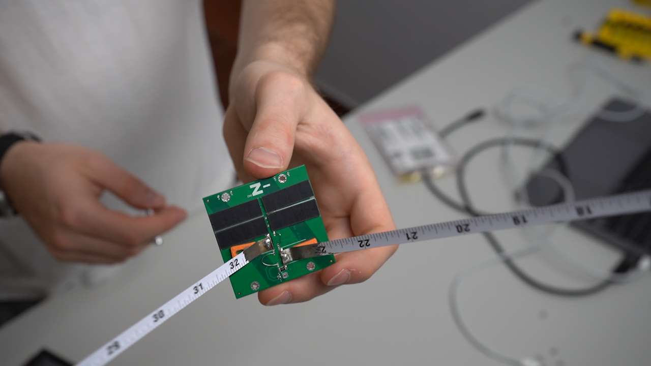
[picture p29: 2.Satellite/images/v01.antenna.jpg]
Creating an antenna (https://youtu.be/2rDQudzhBSQ)


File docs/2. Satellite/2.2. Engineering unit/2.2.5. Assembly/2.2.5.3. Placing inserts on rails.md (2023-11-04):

# Placing inserts on rails

This chapter will describe how to correctly place the heat inserts into the rails.

<br /> 

## What you need

- [Inserts](#heat-inserts);

- [Rails](#rails);

- M2 and M3 drilling machine;

- Soldering iron;

- Sandpaper:

<br />

## Step 1: Place the inserts

- Mount and tightly secure the M3 drill;

- Grab the printed rails and fix them on a vise;

- Drill the four M3 holes on the corners of the -Y board to remove imperfections;

*TIP: with the drill not rotating, align it with hole and then run it.*

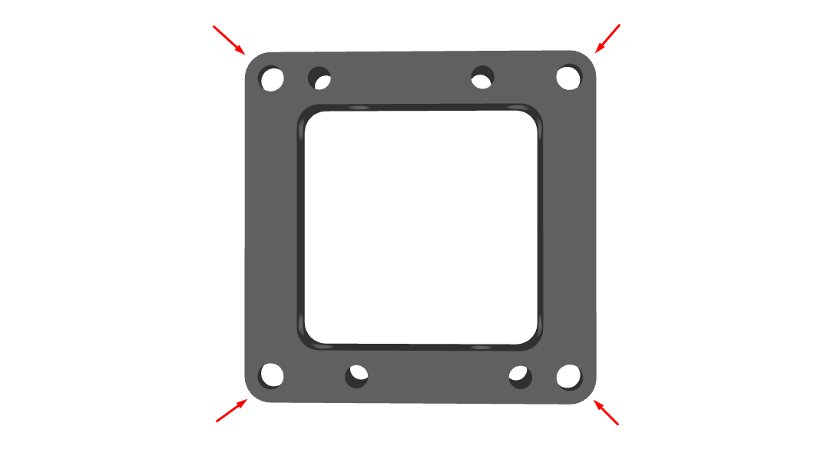
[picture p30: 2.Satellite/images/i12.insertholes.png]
Insert holes


- Repeat the above with a M2 drill in the remaining holes of both boards;

- Turn on the soldering iron at 275 ºC (slighty above the polymer melting point) and let it heat;

- Select the right insert for each hole and figure out its orientation;

*TIP: check the figure to find out the correct orientation.*

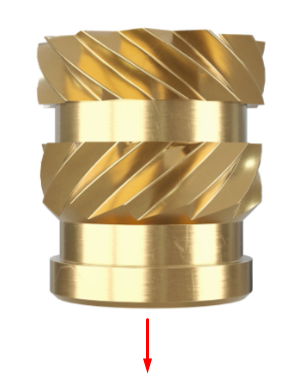
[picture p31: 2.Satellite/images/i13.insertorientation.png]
Insert orientation


- From the outside perspective of the satellite, place each insert on top of the hole and push it down the rail with the iron, until the insert is totally inside;

*TIP: make sure it goes down slowly and straight as the plastic melts.*

<br /> 

## Step 2: Final procedures

- Sand the remaining material off the hole margins and interiors;

- Check if the standoffs and screw can be easily fixed;

- Check if the camera board can be placed on -Y rail and, if needed, sand the side wall to allow it;

<br />

## Video guide

Press on the image to be redirected to view the video guide on YouTube.

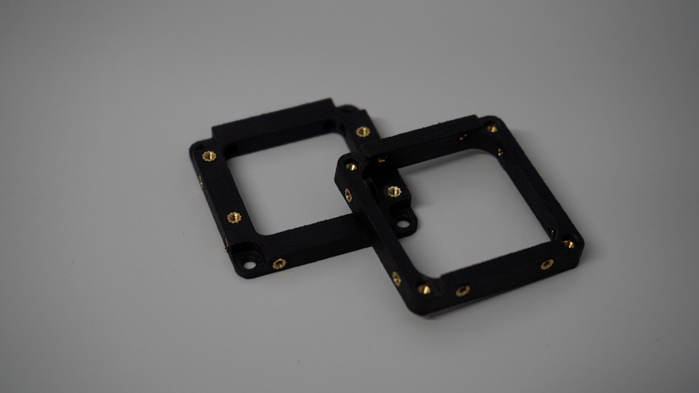
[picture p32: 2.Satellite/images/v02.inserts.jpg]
Placing inserts on rails (https://youtu.be/tuawUfmNegQ)


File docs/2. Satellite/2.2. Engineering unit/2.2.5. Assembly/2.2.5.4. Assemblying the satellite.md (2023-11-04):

# Assemblying the satellite

This chapter will describe the steps required to place the rails, inside and outside boards on the correct order and position on order to assemble the PocketQube. It is recommended to open the CAD assembly file, released in [Mechanical Structure](https://github.com/AFS-pt/PROMETHEUS-1/blob/main/2.Satellite/1.Hardware/Mechanical_Structure), to help visualize it.

<br />

## What you need

- [PCBs](https://afs-pt.github.io/PROMETHEUS-1/2.%20Satellite/2.2.%20Engineering%20unit/2.2.1.%20Hardware/2.2.1.1.%20Printed%20circuit%20boards/), with the [antenna](https://afs-pt.github.io/PROMETHEUS-1/2.%20Satellite/2.2.%20Engineering%20unit/2.2.5.%20Assembly/2.2.5.2.%20Creating%20an%20antenna/) and the camera on place;

- [Rails](https://afs-pt.github.io/PROMETHEUS-1/2.%20Satellite/2.2.%20Engineering%20unit/2.2.1.%20Hardware/2.2.1.3.%20Rails/) with the [inserts](https://afs-pt.github.io/PROMETHEUS-1/2.%20Satellite/2.2.%20Engineering%20unit/2.2.5.%20Assembly/2.2.5.3.%20Placing%20inserts%20on%20rails/) on place;

- [Standoffs and screws](https://afs-pt.github.io/PROMETHEUS-1/2.%20Satellite/2.2.%20Engineering%20unit/2.2.1.%20Hardware/2.2.1.4.%20Standoffs%2C%20inserts%20and%20screws/);

- [Fishing line](https://afs-pt.github.io/PROMETHEUS-1/2.%20Satellite/2.2.%20Engineering%20unit/2.2.1.%20Hardware/2.2.1.2.%20Antenna/);

- 2x LP603443 batteries;

- u.FL male to u.FL male cable;

- Kapton adhesive tape;

- Precision toolkit;

<br />

## Step 1: Place the inside boards and rails

- Start by putting the camera board inside the -Y rail, with the camera pointing towards the inside of the rail;

- Place four M3 (8 mm) standoffs in each corner and screw them;

*TIP: making a cross pattern, screw the standoffs only a couple of times each until they give a lot of resistance*

- Plug the main board onto the camera board by its vertical connectors and make sure it aligns in the corners;

- Again, place four M3 (8 mm) standoffs in each corner and screw them;

- Plug the bottom battery board onto the stack, add four M3 (6 mm) standoffs in each corner and screw them;

- Solder both batteries to the corresponding polarity pads in each face of the middle battery board;

- Fix the batteries and its wires to the board with Kapton adhesive tape;

- Plug the finished middle battery board on top of the current satellite stack;

- Place four M3 (6 mm) standoffs in each corner and screw them;

- Plug the top battery board onto the middle one;

- Place the +Y rail on top of the stack and make sure its inserts match the silk note circles positions in the battery board;

- Screw the rail and board in place with 4 units of M3 (6 mm) screws;

<br />

## Step 2: Add the outside boards

- Carefully connect the u.FL to u.FL antenna cable to the main board connector and leave the other end outside the stack;

- Place -X solar board in its designed face, with solar cells outwards and making sure the placement of the side connector between the board and the stack is correct;

- Screw the board in place with 4x M2 (5 mm) screws, following the same screwing technique as before;

- Repeat the previous points with the +Y and +Z boards;

- Place and screw the -Y board to the -Y rail with 4x M3 (4 mm) screws;

- After that, connect the remaining end of the u.FL cable to the -Z board connector and place the board. Managing the cable through the +X side, certify that it passes through the inside board's hollow space present in the -Z side;

- When completed, screw the board with 4x M2 (5 mm) units;

- Finally, close the satellite with the +X board and screw it with 4x M2 (5 mm) screws;

<br /> 

## Step 3: Tie the antenna

- Tightly wrap the antenna strips around the satellite and temporarily fix them with adhesive tape;

- Cut two pieces of fishing line with around 20 cm long;

*TIP: this length is more than enough but it makes the tying easier.*

- Pass the line through the first antenna tip hole and the first burn wire, tie it with a square knot and cut the surplus;

- Repeat the previous point on the other antenna strip;

<br />

## Video guide

Press on the image to be redirected to view the video guide on YouTube.

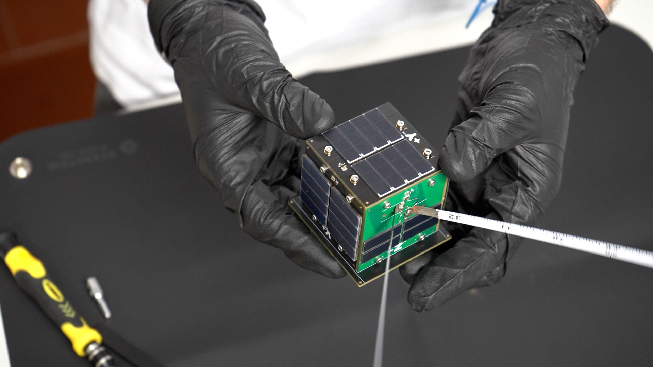
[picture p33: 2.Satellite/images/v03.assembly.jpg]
Assemblying the satellite (https://youtu.be/qyBwiglurZg)


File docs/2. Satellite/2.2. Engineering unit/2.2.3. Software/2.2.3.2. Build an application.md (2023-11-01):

# Build an application

## What you need

- Bash console;
  
- Flight software;  
  
> - python3
>
> - numpy
> 
> - ImageMagick
> 
> - graphviz
>
> *NOTE: Numpy is used for running the emulated sattelite and is therefore not required for building. ImageMagick and graphviz are used to create a state machine diagram along with your built files.*

<br /> 

## Step 1: Run the script

> To build the flight software you run:
> 
> ```bash
> $ sh build.sh {driver} {application}
> ```
>
> The {driver} is the part of the software that interfaces with the hardware (or emulates it).
> 
> The {application} is what the software attempts to achieve the mission objective (by utilizing the driver to communicate with the hardware).
> 
> This allows us to easily test and develop flight software localy by emulating the hardware.

For example, for building system-check app, you should run:
```bash
user@machine ~/Software/Flight/state_machine
$ sh build.sh drivers/pycubedmini/ applications/system-check/
```

The build should appear at `~/Software/Flight/state_machine/build/` directory.

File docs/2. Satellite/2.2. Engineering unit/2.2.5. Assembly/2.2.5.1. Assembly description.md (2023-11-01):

# Assembly description

This chapter states the final assembly of the unit once all the parts required and detailed above are gathered. In order to provide help for those who skipped to this chapter, or just to take extra precaution before this steps, the components and tools needed specifically for each subchapter are detailed at the start of each one. Nevertheless, a prior reading should prepare you for a better and continuous assembly process.

There are also some guidance videos that can help to visualize most of the steps taken, as well as some useful explanations given during the procedures. They are complementary, as all information is available in text.

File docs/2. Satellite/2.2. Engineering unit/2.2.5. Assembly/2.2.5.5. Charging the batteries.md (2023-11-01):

# Charging the batteries

After finishing the assembly, you can charge the satellite via the connector on the back side of the -Y board. For that, plug a BM02B-SRSS-TB male cable and provide around 3.7 V, with a maximum current of 850 mAh until the current drops to the recommended cut-off value.

*NOTE: These voltage and current values were retrieved from the batteries' datasheet. Always check it to make sure you execute the standard charging procedure correctly!*

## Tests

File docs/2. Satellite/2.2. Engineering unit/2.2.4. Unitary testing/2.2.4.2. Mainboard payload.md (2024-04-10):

# Mainboard payload

Based on system check app, which allows to test almost all systems, the same app can be used to validate some of the mainboard components and its connections, such as IMU readings or SD card detection.

<br /> 

## What you need

- Mu Editor

- Flight software;

- Mainboard;

- USB-C cable, with power and data lines;

<br /> 

## Step 1: Install Mu Editor

Based on [AdaFruit tutorial](https://learn.adafruit.com/welcome-to-circuitpython/installing-mu-editor):

> Mu is a simple code editor that works with the Adafruit CircuitPython boards. It's written in Python and works on Windows, MacOS, Linux and Raspberry Pi. The serial console is built right in so you get immediate feedback from your board's serial output!
>
> - Download Mu from its [official website](https://www.codewith.mu);
>
> - Click the Download link for downloads and installation instructions;
>
> *NOTE: Click 'Start Here' to find other useful information, including extensive tutorials and how-to's.*
>
> - The first time you start Mu, you will be prompted to select your 'mode' - in our case, CircuitPython;
>
> *NOTE: Mu attempts to auto-detect your board on startup, so if you do not have a CircuitPython board plugged in with a CIRCUITPY drive available, Mu will inform you where it will store any code you save until you plug in a board.*
>
> - You can now explore Mu: you can use the text editor to edit the files (or use one at your preference) and interface with the main board with the serial console.

*TIP: in serial console, while the mainboard is plugged to your machine, use CTRL+C to stop the current program running on the board and CTRL+D to start the one on the volume. If the 'resource is busy' alert pops up, reconnect the board.*

<br /> 

## Step 2: Test the mainboard

- Build (following the [steps](https://afs-pt.github.io/PROMETHEUS-1/2.%20Satellite/2.2.%20Engineering%20unit/2.2.3.%20Software/2.2.3.2.%20Build%20an%20application/) above) and copy the system check files to the CIRCUITPY board;

- Open Mu Editor serial console and start running the program (CTRL+D);

- Follow the serial prompt, typing the code word for each specific test to be run.

You have 8 tests in total available in this application, however only 3 can help you to validade in this phase (IMU, NVM, SD).

Later in the guide, in [System check](https://afs-pt.github.io/PROMETHEUS-1/2.%20Satellite/2.2.%20Engineering%20unit/2.2.6.%20System%20check/2.2.6.1.%20System%20check%20description/) chapter, there is a detailed overview of this application, with the description of each test and expected result.

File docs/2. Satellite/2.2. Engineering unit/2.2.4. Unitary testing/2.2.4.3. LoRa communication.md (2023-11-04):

# LoRa communication

Another test that can be performed is the correct sending or receiving of LoRa packets. This can only be achieved while main board and antenna (-Z) board are connected, which is extremely important, since the absence of an antenna (load) may damage the trasmitter due to wave (power) reflection implying voltage and current overloads [[1]](https://electronics.stackexchange.com/questions/335912/can-i-break-a-radio-tranceiving-device-by-operating-it-with-no-antenna-connected).

The test software is released in [Tests](https://github.com/AFS-pt/PROMETHEUS-1/blob/main/2.Satellite/3.Software/Tests/), and is already built. To fully test, a second device is needed to check if the satellite is either able to successfully send of receive the packets. It can be another satellite (with both using the same test files) or a groundstation, composed of a ESP-32 or Raspberry Pi microcontroller with a compatible LoRa chip.

During testing phase, we had all the options stated: [LILYGO® TTGO T-Beam v1.1](https://meshtastic.org/docs/hardware/devices/tbeam/), a ESP-32 based groundstation; and RExLab custom groundstation, RPi based; and another twin satellite. We will cover the first case since it can be more easily replicated, either with a similar designed board or just with a simple ESP-32/Arduino connected to a LoRa IC.

<br />  

## What you need

- Mu Editor and Arduino IDE;

- Lora Radio Range Test files;

- Main and -Z board;

- u.FL male to u.FL male cable;

- USB-C cable, with power and data lines;

- Another LoRa device for validation;

<br /> 

## Step 1: Configure the groundstation for sending

- After installing Arduino IDE, install the ESP32 board drivers (follow this [tutorial](https://randomnerdtutorials.com/installing-the-esp32-board-in-arduino-ide-windows-instructions/)). In our case, the board reference changes to 'TTGO LoRa32-OLED' and the COM port may be defined to another instance;

- Install the libraries needed for peripherals, such as the OLED and LoRa chip (follow this [tutorial](https://randomnerdtutorials.com/ttgo-lora32-sx1276-arduino-ide/));

- Create a project with the sender sketch from the last tutorial, compile, run and open Serial Viewer, configured with the correct parameters. Again, in our case, change the board pins (MISO, SDA, ...) to the correct board [pinout](https://meshtastic.org/assets/images/t-beam_v1.1_pinmap-7c3402af077cdf2a5f90645561e049dc.webp) and frequency (433 MHz);

- The OLED should display the init prompt and the board starting to send packets.

Test setup

<br /> 

## Step 2: Set the satellite for receiving

- Connect the main and -Z boards with the u.FL cable;

- Like the previous unitary test, copy the files to the mainboard, open Mu Editor serial console and start running the program (CTRL+D);

- Follow the serial prompt, selecting the satellite option, followed by the radio parameters change (the default options should be fine);

- Finally, you should set the receiving mode with acknowledge;

- In a few seconds, it should print the received LoRa packet info, such as the RSSI and the message;

Serial viewer

<br /> 

## Step 3: Invert the communication direction

To make the groundstation for Rx mode, you can simply use the receiver sketch instead of the sender one, also released in the previous [tutorial website](https://randomnerdtutorials.com/ttgo-lora32-sx1276-arduino-ide/) and switch the satellite to Tx mode on prompt.

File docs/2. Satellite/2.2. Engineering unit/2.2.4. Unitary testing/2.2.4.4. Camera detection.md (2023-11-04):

# Camera detection

After the camera installation on the board, it is possible to transmit live video to a computer through USB, checking the correct functioning of the components and the firmware.

<br /> 

## What you need

- OpenMV IDE;

- Camera board;

- USB-C cable, with power and data lines;

<br /> 

## Step 1: Test the camera

- After installing OpenMV IDE, connect the camera board with the USB-C cable to your computer and open the IDE;

- On the top navigation bar, click in "File", "Examples", "HelloWorld" and "helloworld.py";

- If the board was detected, on the bottom left corner, click in the image buttons "Connect" and then "Start". If not, a brief troubleshooting should appear to unbrick your board;

- After this, you should get live feed from your camera at the top right corner;

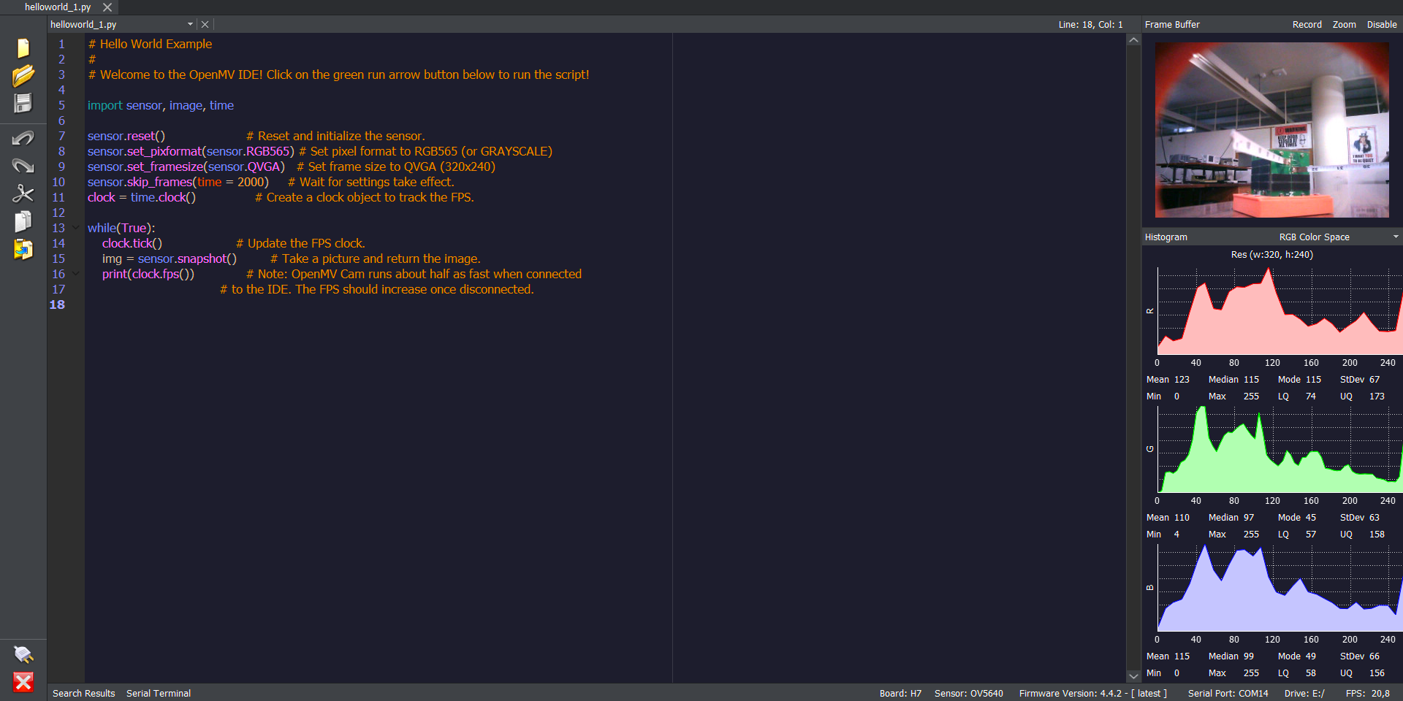
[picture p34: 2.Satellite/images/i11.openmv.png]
Open MV


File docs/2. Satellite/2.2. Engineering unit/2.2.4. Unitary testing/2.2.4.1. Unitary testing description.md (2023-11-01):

# Unitary testing

By unitary testing, we refer to simple tests that can and should be made before assembling an entire unit. These can detect some errors or damages when testing individuals systems, for example, on communication or board detections. In this chapter, there are some detailed steps and expected results to be achieved during this type of testing.

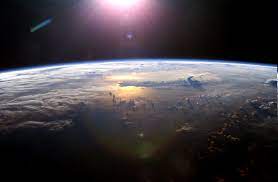
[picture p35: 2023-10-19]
3.GroundStation/GS_UMinho/GS_TinyGS/Testing/Telemetry and Image Decoder/image.png

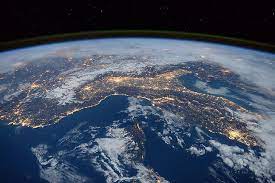
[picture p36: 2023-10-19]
3.GroundStation/GS_UMinho/GS_TinyGS/Testing/Telemetry and Image Decoder/result.jpeg

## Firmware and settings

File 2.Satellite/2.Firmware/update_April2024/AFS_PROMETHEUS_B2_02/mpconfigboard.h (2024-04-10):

#define MICROPY_HW_BOARD_NAME "AFS_PROMETHEUS_B2_02"//"PyCubedMini"
#define MICROPY_HW_MCU_NAME "samd51j19"
#define CIRCUITPY_MCU_FAMILY samd51

#define MICROPY_HW_NEOPIXEL   (&pin_PA21)

#define MICROPY_PORT_A        (PORT_PA08 | PORT_PA09 | PORT_PA10 | PORT_PA11)
#define MICROPY_PORT_B        ( PORT_PB10 | PORT_PB11)
#define MICROPY_PORT_C        (0)
#define MICROPY_PORT_D 		  (0)

#define SPI_FLASH_WP_PIN            &pin_PA10
#define SPI_FLASH_HOLD_PIN          &pin_PA11

// External flash MR2xH40 MRAM
#define EXTERNAL_FLASH_QSPI_SINGLE
#define EXTERNAL_FLASH_NO_JEDEC

#define AUTORESET_DELAY_MS 500

#define BOARD_HAS_CRYSTAL 1

#define DEFAULT_I2C_BUS_SCL  (&pin_PB13)
#define DEFAULT_I2C_BUS_SDA  (&pin_PB12)

#define DEFAULT_SPI_BUS_SCK  (&pin_PA13)
#define DEFAULT_SPI_BUS_MOSI (&pin_PA12)
#define DEFAULT_SPI_BUS_MISO (&pin_PA14)

#define IGNORE_PIN_PA24     1
#define IGNORE_PIN_PA25     1

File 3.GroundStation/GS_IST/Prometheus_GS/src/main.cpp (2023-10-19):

#include "Arduino.h"
#include "WiFi.h"
#include "ESPAsyncWebServer.h"
#include "AsyncWebSocket.h"
#include "libraries/decoder.h"
#include <libraries/LORA.h>
#include <SPI.h>
#include <ESP32Servo.h>
#include <ArduinoJson.h>
#include <sstream>
#include "kaitai/kaitaistruct.h"
#include <iostream>
#include <cstring>
#include <StreamString.h>


#define pingo 34          // pin for push-button
#define pinf  2          // pin for signaling led
#define azimuth_pin 25
#define elevation_pin 27

#define MESS "Simple test message"    // message to send and receive
#define RXTIMEOUT 500    // tens of milliseconds (I.E. RXTIMEOUT*10=milliseconds)
#define inplen 64        // sending buffer len 
#define reclen 255        // receiving buffer len 



LORA LR;                 // Class LORA instance

unsigned dest;
char msg[inplen];
char inpbuff[inplen];    // sending buffer
char recbuff[reclen];    // receiving buffer
int cnt=0;
float azimuth, elevation;
Servo servoAzimuth, servoElevation;
char data[64];           // buffer for RSSI and SNR
#define format "|Rssi: %d RssiPk: %d SnrPk %d|  "

int SF=9;  //Spreading factor value (if changed for test)
int BW=6;  //Bandwidth value (if changed for test)

int PWR=5; //transmit power (100mW)

boolean SHIELD=true;
boolean getInput();
void sendBuff();
void getReplay();
void blinkpinf(int time,int n);
void showConfig();
boolean getSerialMsg();
boolean sendSerialMsg();
boolean sendWifiMsg();
int nb;
void onWsEvent_rot(AsyncWebSocket* server, AsyncWebSocketClient* client, AwsEventType type, void* arg, uint8_t* data, size_t len);
void onWsEvent_cmd(AsyncWebSocket* server, AsyncWebSocketClient* client, AwsEventType type, void* arg, uint8_t* data, size_t len);

char terminal_buffer[1024];

void readPayload(prometheus_t* datastream);

// Access Point 
const char* ssid = "PROMETHEUS";
const char* password = "VerySecurePW";
AsyncWebServer server(80);
AsyncWebSocket ws_rotator("/rot_ws");
AsyncWebSocket ws_command("/cmd_ws");
WiFiClient client;
bool wifi_flag = false;
bool angle_flag = false;



const char index_html[] PROGMEM = R"rawliteral(
<!DOCTYPE HTML><html>
<head>
  <title>Prometheus GS</title>
  <meta name="viewport" content="width=device-width, initial-scale=1">
  <link rel="icon" href="data:,">
  <style>
  html {
    font-family: Arial, Helvetica, sans-serif;
    text-align: center;
  }
  h1 {
    font-size: 1.8rem;
    color: white;
  }
  h2{
    font-size: 1.5rem;
    font-weight: bold;
    color: #143642;
  }
  .topnav {
    overflow: hidden;
    background-color: #143642;
  }
  body {
    margin: 0;
  }
  .content {
    padding: 30px;
    max-width: 600px;
    margin: 0 auto;
  }
  .card {
    background-color: #F8F7F9;;
    box-shadow: 2px 2px 12px 1px rgba(140,140,140,.5);
    padding-top:10px;
    padding-bottom:20px;
  }
  .button {
    padding: 15px 50px;
    font-size: 24px;
    text-align: center;
    outline: none;
    color: #fff;
    background-color: #0f8b8d;
    border: none;
    border-radius: 5px;
    -webkit-touch-callout: none;
    -webkit-user-select: none;
    -khtml-user-select: none;
    -moz-user-select: none;
    -ms-user-select: none;
    user-select: none;
    -webkit-tap-highlight-color: rgba(0,0,0,0);
   }
   /*.button:hover {background-color: #0f8b8d}*/
   .button:active {
     background-color: #0f8b8d;
     box-shadow: 2 2px #CDCDCD;
     transform: translateY(2px);
   }
   .cmd-label{
    font-size: 1.1rem;
    color:#143642;
    font-weight: bold;
   }
   input.cmd{
    background: #ecf0f3;
    padding-top: 5px;
    padding-left: 10px;
    height: 30px;
    width: 300px;
    font-size: 14px;
    border-radius: 50px;
    }
    input.submit{
    background: #0f8b8d;
    text-align: center;
    padding: auto;
    height: 30px;
    width: 70px;
    font-size: 14px;
    border-radius: 50px;
    }
    .angles{
      display: flex;
      font-size: 1.5rem;
      color:#8c8c8c;
      font-weight: bold;
    }
    .angle{
      flex: 1;
    }
    .angle-number{
      font-size: 3rem;
    }
  </style>
<title>PROMETHEUS GroundStation</title>
<meta name="viewport" content="width=device-width, initial-scale=1">
<link rel="icon" href="data:,">
</head>
<body>
  <div class="topnav">
    <h1>PROMETHEUS GroundStation</h1>
  </div>
  <div class="content">
    <div class="card">
      <h2>Terminal</h2>
      <div id="cmd_box" style="height:150px;width:500px;border:1px solid #ccc;font:16px/26px;font-family: 'Courier New', monospace;overflow:auto;margin: auto;text-align: left;">
        <span id="strings"><br></span>  
      </div><br>
      <form id="cmd-form">
        <label class="cmd-label"> Command: </label>
        <input class="cmd" type="text" name="cmd" id="cmd-input">
        <input class="submit" type="submit" value="Send" onclick="getCmd()">
      </form><br>  
      <div class="angles" style="margin: auto;">
        <div class="angle">
          <span id="az" class="angle-number"></span>
          <br><label>Azimuth</label>
        </div>
        <div class="angle">
          <span id="el" class="angle-number"></span>
          <br><label>Elevation</label>
        </div>
      </div>
    </div>
    
  </div>
  
<script>
  var terminal = "---";
  var rot_gateway = `ws://${window.location.hostname}/rot_ws`;
  var cmd_gateway = `ws://${window.location.hostname}/cmd_ws`;
  var rot_websocket, cmd_websocket;
  window.addEventListener('load', onLoad);
  function initWebSocket() {
    console.log('Trying to open a WebSocket connection...');
    
    rot_websocket = new WebSocket(rot_gateway);
    rot_websocket.onopen    = onOpen;
    rot_websocket.onclose   = onClose;
    rot_websocket.onmessage = onRotMessage;

    cmd_websocket = new WebSocket(cmd_gateway);
    cmd_websocket.onopen    = onOpen;
    cmd_websocket.onclose   = onClose;
    cmd_websocket.onmessage = onCmdMessage;
  }
  function onOpen(event) {
    console.log('Connection opened');
  }
  function onClose(event) {
    console.log('Connection closed');
    setTimeout(initWebSocket, 2000);
  }
  function onRotMessage(event) {
    var angles = event.data.split(" ");
    
    document.getElementById('az').innerHTML = angles[0];
    document.getElementById('el').innerHTML = angles[1];
  }

  function onCmdMessage(event) {
    document.getElementById('strings').innerHTML += event.data + '<br>';
    var objDiv = document.getElementById("cmd_box");
    objDiv.scrollTop = objDiv.scrollHeight;
  }
  function onLoad(event) {
    initWebSocket();
    initButton();
  }
  
  function getCmd() {
    var prompt = document.getElementById("cmd-input").value;
    document.getElementById('strings').innerHTML += ('<a style="color:#4673a3";>$ ' + prompt + '</a> <br>');
    cmd_websocket.send(prompt);

    var objDiv = document.getElementById("cmd_box");
    objDiv.scrollTop = objDiv.scrollHeight;
  }

  var form = document.getElementById("cmd-form");
  
  form.addEventListener("submit", function(event) {
    event.preventDefault(); // Prevent the form from submitting normally
    //getCmd();
    document.getElementById("cmd-input").value = "";
  });


</script>
</body>
</html>
)rawliteral";


bool ledState = 0;

void updateRotators() {
  ws_rotator.textAll(String(azimuth)+' '+String(elevation));
}

void updateTerminal(String str) {
  ws_command.textAll(str);
}

void WsMsgHandler_rot(void *arg, uint8_t *data, size_t len) {
  AwsFrameInfo *info = (AwsFrameInfo*)arg;
  int i=0;
  String s;
  StaticJsonDocument<200> doc;
  DeserializationError error = deserializeJson(doc, data);
  if (info->final && info->index == 0 && info->len == len && info->opcode == WS_TEXT) {
      Serial.printf("DATA---> %s\n", data);
      if (error) {
        Serial.print(F("deserializeJson() failed: "));
        Serial.println(error.f_str());
        return;
      } else {
        const float az_val = doc["azimuth"];
        const float el_val = doc["elevation"];
        Serial.println(az_val);
        Serial.println(el_val);

        azimuth = az_val;
        elevation = el_val;
      }

      updateRotators();
      angle_flag = true;
  }
}

void WsMsgHandler_cmd(void *arg, uint8_t *data, size_t len) {
  AwsFrameInfo *info = (AwsFrameInfo*)arg;
  char buff[64];
  snprintf(buff, len+1, "%s", data, len);
  if (info->final && info->index == 0 && info->len == len && info->opcode == WS_TEXT) {
      Serial.printf("DATA---> %s          [%d]\n", buff, len);
  }
  strlcpy(msg, buff, inplen);
  Serial.println(msg);
  wifi_flag = true;
}

String processor(const String& var){
  Serial.println(var);
  if(var == "STATE"){
    if (ledState){
      return "ON";
    }
    else{
      return "OFF";
    }
  }
  return String();
}


typedef struct{
  uint8_t header[4];
  uint8_t packet_id;
  uint8_t payload[250];
}packet_t;

void printKStreamBytes(kaitai::kstream* ks, size_t numBytes) {
    for (int i = 0; i < numBytes; ++i) {
        uint8_t byteValue = ks->read_u1();
        //std::cout << "Byte " << i << ": " << std::hex << static_cast<int>(byteValue) << std::endl;
        Serial.printf("Byte %d: 0x%x\n", i, byteValue);
    }
}

void setup() 
{
  Serial.begin(115200);
  pinMode(pingo,INPUT);
  pinMode(pinf,OUTPUT); digitalWrite(pinf,0);
  servoAzimuth.attach(azimuth_pin);
  servoElevation.attach(elevation_pin);

  Serial.print("Setting AP (Access Point)…");
  // Remove the password parameter, if you want the AP (Access Point) to be open
  WiFi.softAP(ssid, password);

  IPAddress IP = WiFi.softAPIP();
  Serial.print("AP IP address: ");
  Serial.println(IP);

//....................................................................
  server.on("/", HTTP_GET, [](AsyncWebServerRequest *request){
    request->send(200, "text/html", index_html); 
  });

  server.on("/get", HTTP_GET, [] (AsyncWebServerRequest *request) {
    String inputMessage;
    String inputParam;
    
    // GET cmd value on <ESP_IP>/get?cmd=<inputMessage>
    if (request->hasParam("cmd")) {
      inputMessage = request->getParam("cmd")->value();
      inputParam = "cmd";
      //ws_command.textAll(inputMessage);
      wifi_flag = true;
    }
    else if (request->hasParam("az")) {
      inputMessage = request->getParam("az")->value();
      inputParam = "az";
      azimuth = inputMessage.toFloat();
      Serial.print("AZIMUTH: ");
      Serial.println(azimuth);
      angle_flag = true;
    } 
    else if (request->hasParam("el")) {
      inputMessage = request->getParam("el")->value();
      inputParam = "el";
      elevation = inputMessage.toFloat();
      Serial.print("ELEVATION: ");
      Serial.println(elevation);
      angle_flag = true;
    } 
    else {
      inputMessage = "No message sent";
      inputParam = "none";
    }

    strcpy(msg, inputMessage.c_str());
    //Serial.println(inputMessage);
    
    //request->send(200, "text/html", "HTTP GET request sent to your ESP on input field (" 
    //                                 + inputParam + ") with value: " + inputMessage +
    //                                 "<br><a href=\"/\">Return to Home Page</a>");
    
    request->redirect("/");
  });


  server.addHandler(&ws_rotator);
  ws_rotator.onEvent(onWsEvent_rot);

  server.addHandler(&ws_command);
  ws_command.onEvent(onWsEvent_cmd);

  server.begin();


//....................................................................


  if (!LR.begin()) 
    {Serial.println("No LoRa shield detected! Stop!");SHIELD=false;return;}
  Serial.println("LoRa echo transmitter.");
  SX.setPower(PWR);
//LR.setConfig(SF,BW,4);       // if you want test different configuration (def: 9,6,4)
  showConfig();
  strlcpy(inpbuff,MESS,inplen);
  Serial.print("Close pin ");Serial.print(pingo);Serial.println(" to ground to send message");  
  LR.receiveMessMode();
}

void loop() 
{
  delay(200);
  if (!SHIELD) return;
  if (getInput()) {sendBuff();getReplay();}
  if ((nb=getSerialMsg())>0) {
    Serial.println("OK");
    if (sendSerialMsg())getReplay();
    //updateTerminal(recbuff);
  }
  if (wifi_flag){
    wifi_flag = false;
    if (sendSerialMsg())getReplay();
    //updateTerminal(recbuff);
  } 
  else if (LR.dataRead(recbuff,reclen)>0){
    Serial.println("Got something: ");
    //std::istringstream is(recbuff);
    //kaitai::kstream ks(&is);
    //kaitai::kstruct kst(&ks);
//    char buffer[] = {171, 186, 10, 10, 0, 204, 204, 204, 61, 204, 204, 76, 62, 152, 153, 153, 62, 204, 204, 204, 61, 204, 204, 76, 62, 152, 153, 153, 62, 204, 204, 204, 61, 204, 204, 76, 62, 152, 153, 153, 62, 0, 0, 240, 65, 21, 0, 22, 0, 23, 0, 11, 0, 12, 0, 13, 0, 100, 102, 134, 64, 48, 51, 243, 65};
    //char buffer[] = {171, 186, 0, 0, 10, 1, 85, 85, 85, 85, 85, 85, 85, 85, 85, 85, 85, 85, 85, 85, 85, 85, 85, 85, 85, 85, 85, 85, 85, 85, 85, 85, 85, 85, 85, 85, 85, 85, 85, 85, 85, 85, 85, 85, 85, 85, 85, 85, 85, 85, 85, 85, 85, 85, 85, 85, 85, 85, 85, 85, 85, 85, 85, 85, 85, 85, 85, 85, 85, 85, 85, 85, 85, 85, 85, 85, 85, 85, 85, 85, 85, 85, 85, 85, 85, 85, 85, 85, 85, 85, 85, 85, 85, 85, 85, 85, 85, 85, 85, 85, 85, 85, 85, 85, 85, 85, 85, 85, 85, 85, 85, 85, 85, 85, 85, 85, 85, 85, 85, 85, 85, 85, 85, 85, 85, 85, 85, 85, 85, 85, 85, 85, 85, 85, 85, 85, 85, 85, 85, 85, 85, 85, 85, 85, 85, 85, 85, 85, 85, 85, 85, 85, 85, 85, 85, 85, 85, 85, 85, 85, 85, 85, 85, 85, 85, 85, 85, 85, 85, 85, 85, 85, 85, 85, 85, 85, 85, 85, 85, 85, 85, 85, 85, 85, 85, 85, 85, 85, 85, 85, 85, 85, 85, 85, 85, 85, 85, 85, 85, 85, 85, 85, 85, 85, 85, 85, 85, 85, 85, 85, 85, 85, 85, 85, 85, 85, 85, 85, 85, 85, 85, 85, 85, 85, 85, 85, 85, 85, 85, 85, 85, 85, 85, 85, 85, 85, 85, 85, 85, 85, 85, 85, 85, 85, 85, 85, 85, 85, 85, 85, 85, 85, 85, 85, 85, 85};
    //char* buffer; strcpy(buffer, recbuff);
    //size_t buffer_size = sizeof(buffer);

    for(int i=0; i<reclen; i++){
      Serial.printf("%x, ", recbuff[i]);
    }

    for(int i=0; i<reclen; i++){
      Serial.printf("%x, ", recbuff[i]);
    }

    std::istringstream stream(std::string(recbuff, reclen));

    // Create a kaitai::kstream from the Stream
    kaitai::kstream ks(&stream);
    //printKStreamBytes(&ks, buffer_size);

  
    packet_t *pckt = (packet_t *) recbuff;   
    Serial.printf("LENGTH: %d\n", reclen); 
    Serial.printf("Header[%x,%x,%x,%x] ID:%x \n", pckt->header[0], pckt->header[1], pckt->header[2], pckt->header[3], pckt->header[4], pckt->packet_id);

    delay(100); Serial.println("Parsing Packet ");
    
    Serial.println("------------------------");

    prometheus_t* datastream = NULL;

    try {
      datastream = new prometheus_t(&ks);

      Serial.printf("HEADER DESTINATION: 0x%x\n", datastream->header()->destination());
      Serial.printf("HEADER NODE:        0x%x\n", datastream->header()->node());
      Serial.printf("HEADER IDENTIFIER:  0x%x\n", datastream->header()->identifier());
      Serial.printf("HEADER FLAGS:       0x%x\n", datastream->header()->flags());
      Serial.printf("PACKET ID: %d\n", datastream->packet_id());

    } catch(const std::exception& e){
      Serial.println(e.what());
    }
    
    readPayload(datastream);
    
    Serial.println("------------------------");
    
    //int id = packet.packet_id();
    
    //for(int i=0; i < buffer_size; i++){
    //  Serial.printf("%x,", recbuff[i]);
    //}
    //updateTerminal(recbuff);
  }

  if (angle_flag){
    angle_flag = false;
    if (azimuth>180){azimuth = 180;} 
    else if (azimuth < 0) {azimuth = 0;}
    if (elevation>180){elevation = 180;} 
    else if (elevation < 0) {elevation = 0;}
    servoAzimuth.write((int)azimuth);
    servoElevation.write((int)elevation);
    updateRotators();
  }
  
  ws_rotator.cleanupClients();
}




void onWsEvent_rot(AsyncWebSocket *server, AsyncWebSocketClient *client, AwsEventType type,
             void *arg, uint8_t *data, size_t len) {
  switch (type) {
    case WS_EVT_CONNECT:
      Serial.printf("WebSocket client #%u connected from %s\n", client->id(), client->remoteIP().toString().c_str());
      break;
    case WS_EVT_DISCONNECT:
      Serial.printf("WebSocket client #%u disconnected\n", client->id());
      break;
    case WS_EVT_DATA:
      WsMsgHandler_rot(arg, data, len);
      Serial.printf("DATA on the websocket\n");
      break;
    case WS_EVT_PONG:
    case WS_EVT_ERROR:
      break;
  }
}



void onWsEvent_cmd(AsyncWebSocket *server, AsyncWebSocketClient *client, AwsEventType type,
             void *arg, uint8_t *data, size_t len) {
  switch (type) {
    case WS_EVT_CONNECT:
      Serial.printf("WebSocket client #%u connected from %s\n", client->id(), client->remoteIP().toString().c_str());
      break;
    case WS_EVT_DISCONNECT:
      Serial.printf("WebSocket client #%u disconnected\n", client->id());
      break;
    case WS_EVT_DATA:
      WsMsgHandler_cmd(arg, data, len);
      Serial.printf("DATA on the websocket\n");
      break;
    case WS_EVT_PONG:
    case WS_EVT_ERROR:
      break;
  }
}


boolean getInput()
{
  if (digitalRead(pingo)) return false;
  return true;
}

void sendBuff()
{
  blinkpinf(100,10);
  digitalWrite(pinf,LOW);
  sprintf(inpbuff, "%s:%3d\n", MESS, cnt++);
  Serial.print("> ");Serial.println(inpbuff);
  int f=LR.sendMess(inpbuff); 
  if (f<0) Serial.println("Error in transmission!");

  SX.setState(STDBY);
}

boolean sendSerialMsg()
{
  Serial.print("To ");Serial.print(dest);Serial.print(" > ");Serial.println(msg);
  char packet[64];
  char header[5];
  /*header[0] = 0xab;
  header[1] = 0xba;
  header[2] = '0';
  header[3] = '0';
  header[4] = 0;
  strcpy(packet, header);
  strcat(packet, msg);*/
  Serial.print(strlen(msg));
  int f=LR.sendMess(msg); 
  if (f<0) Serial.println("Error in transmission!");
  else Serial.println("Sent...");
  SX.setState(STDBY);
  return true;
}


void getReplay()
{
  LR.receiveMessMode();
  boolean OK=false;
  int i;
  for (i=0;i<RXTIMEOUT;i++)
    {if (LR.dataRead(recbuff,reclen)>0) {OK=true;break;} delay(10);}
  if (!OK) {Serial.println("No replay!");blinkpinf(50,20);return;}
  snprintf(data,63,format,SX.getLoraRssi(),SX.lastLoraPacketRssi(),SX.lastLoraPacketSnr());
  Serial.println(data);
  Serial.print("< ");Serial.println(recbuff); 
  int inc=strlen(inpbuff);
  if (strncmp(recbuff,inpbuff,inc)==0) {digitalWrite(pinf,HIGH);}
  else {blinkpinf(500,4);}
  updateTerminal(recbuff);
}


void blinkpinf(int time,int n)
{
  int i;
  byte p=1;
  for (i=0;i<n;i++) {digitalWrite(pinf,p);delay(time); p=p^1;}
  digitalWrite(pinf,0);
}

void showConfig()
{
  Serial.print("Replay timeout (millisec.): ");Serial.println(RXTIMEOUT*10); 
  Serial.print("Frequence: ");Serial.println(SX.readFreq()); 
  Serial.print("Transmit power (mW): ");Serial.println(SX.getPower(3)); 
  Serial.print("Preamble bytes: ");Serial.print(SX.getLoraPreambleLen());Serial.println("+4"); 
  snprintf(data,63,"SpFactor: %d BandW: %d Cr: %d",SX.getLoraSprFactor(),SX.getLoraBw(),SX.getLoraCr()); 
  Serial.println(data); 
  Serial.print("Rate (byte/sec): ");Serial.println(SX.getSRate());
}


boolean getSerialMsg()
{
  if (Serial.available()==0) return 0;
  String str = Serial.readString();
  
  const char* str1=str.c_str();
  strcpy(msg, str1); 
  int nb=strlen(str1);
  Serial.println("---------------------" + str + " " + nb + "---------------------------");
  
  return nb;
}


boolean sendWifiMsg()
{
  int f=LR.sendMess(msg); 
  if (f<0) Serial.println("Error in transmission!");
  else Serial.println("Sent WiFi Message...");
  SX.setState(STDBY);
  return true;
}

void readPayload(prometheus_t* datastream){
  kaitai::kstruct* payload = datastream->payload();
  
  if (datastream->packet_id() == 0) {
    prometheus_t::telemetry_t* tlm = (prometheus_t::telemetry_t*) payload;

    Serial.println("===ACCEL===");
    Serial.printf("x: %f\n", tlm->imu()->accel_x());
    Serial.printf("y: %f\n", tlm->imu()->accel_y());
    Serial.printf("z: %f\n", tlm->imu()->accel_z());

    Serial.println("===GYRO===");
    Serial.printf("x: %f\n", tlm->imu()->gyro_x());
    Serial.printf("y: %f\n", tlm->imu()->gyro_y());
    Serial.printf("z: %f\n", tlm->imu()->gyro_z());

    Serial.println("===MAG===");
    Serial.printf("x: %f\n", tlm->imu()->mag_x());
    Serial.printf("y: %f\n", tlm->imu()->mag_y());
    Serial.printf("z: %f\n", tlm->imu()->mag_z());


    Serial.println("\n===SUN SENSORS===");
    Serial.printf("X+: %d \t X-: %d\n", tlm->sun_sensor()->sun_xp(), tlm->sun_sensor()->sun_xn());
    Serial.printf("Y+: %d \t Y-: %d\n", tlm->sun_sensor()->sun_yp(), tlm->sun_sensor()->sun_yn());
    Serial.printf("Z+: %d \t Z-: %d\n", tlm->sun_sensor()->sun_zp(), tlm->sun_sensor()->sun_zn());


    Serial.println();
    Serial.printf("VBATT: %f\n", tlm->vbatt());
    Serial.printf("CPU TEMP: %f\n", tlm->cpu_temp());
  }
  else {
    prometheus_t::image_t* img = (prometheus_t::image_t*) payload;
    Serial.println("THIS IS AN IMAGE SEGMENT");
    //Serial.println(img);
  }

}

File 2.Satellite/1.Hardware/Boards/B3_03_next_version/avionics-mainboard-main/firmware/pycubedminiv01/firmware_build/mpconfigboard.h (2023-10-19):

#define MICROPY_HW_BOARD_NAME "PyCubedMini"
#define MICROPY_HW_MCU_NAME "samd51G19"
#define CIRCUITPY_MCU_FAMILY samd51

#define MICROPY_HW_NEOPIXEL   (&pin_PB22)

#define MICROPY_PORT_A        (0)
#define MICROPY_PORT_B        (0)
#define MICROPY_PORT_C        (0)
#define MICROPY_PORT_D 		  (0)

#define CALIBRATE_CRYSTALLESS (0)
#define CIRCUITPY_INTERNAL_NVM_SIZE 1024
#define CIRCUITPY_INTERNAL_FLASH_FILESYSTEM_SIZE (128*1024)

// #define BOARD_FLASH_SIZE (FLASH_SIZE - 0x4000 - 0x0100000)

#define DEFAULT_I2C_BUS_SCL  (&pin_PA16)
#define DEFAULT_I2C_BUS_SDA  (&pin_PA17)

#define DEFAULT_SPI_BUS_SCK  (&pin_PA09)
#define DEFAULT_SPI_BUS_MOSI (&pin_PA08)
#define DEFAULT_SPI_BUS_MISO (&pin_PA10)

#define IGNORE_PIN_PA24     1
#define IGNORE_PIN_PA25     1

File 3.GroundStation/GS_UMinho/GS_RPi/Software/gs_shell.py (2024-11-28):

"""
Provides a basic shell-like interface to send and receive data from the satellite
"""
import sys  # noqa
sys.path.append("lib")  # noqa

from shell_utils import *
from gs_shell_tasks import *
from gs_setup import *
from lib.rxtx_switch import RXTXSwitch
import tasko

try:
    import supervisor
except ImportError:
    supervisor = None


# prevent board from reloading in the middle of the test
if supervisor is not None:
    supervisor.disable_autoreload()

prompt_options = {"Receive loop": ("r", "receive"),
                  "Beacon request loop": ("b", "beacon"),
                  "Image request loop": ("i", "image"),
                  "Upload file": ("u", "upload"),
                  "Request file": ("rf", "request"),
                  "Send command": ("c", "command"),
                  "Set time": ("st", "settime"),
                  "Get time": ("gt", "gettime"),
                  "Help": ("h", "print_help"),
                  "Toggle verbose debug prints": ("v", "verbose"),
                  "Reconfigure radio": ("config",),
                  "Quit": ("q", "quit")}
flattend_prompt_options = [v for pov in prompt_options.values() for v in pov]


def print_help():
    print(f"\n{yellow}Groundstation shell help:{normal}")
    for po in prompt_options:
        print(f"{bold}{po}{normal}: {prompt_options[po]}")

# setup


def gs_shell_radio_setup():
    board_str = get_input_discrete(
        f"""Select the board/radio:
            {bold}(s){normal} satellite,
            {bold}(f){normal} feather,
            {bold}(p){normal} raspberry pi,
            {bold}(t){normal} RPiGS TX,
            {bold}(r){normal} RPiGS RX,
            {bold}(c){normal} RPiGS TX and RX (dual radio),
            {bold}(o){normal} RPiGS TX and RX (single radio),
            """,
        ["s", "f", "p", "t", "r", "c", "o"]
    )

    if board_str == "s":
        spi, cs, reset = satellite_spi_config()
        radio = initialize_radio(spi, cs, reset)
        print(f"{bold}{green}Satellite{normal} selected")
    elif board_str == "f":
        spi, cs, reset = feather_spi_config()
        radio = initialize_radio(spi, cs, reset)
        print(f"{bold}{green}Feather{normal} selected")
    elif board_str == "p":
        spi, cs, reset = pi_spi_config()
        radio = initialize_radio(spi, cs, reset)
        print(f"{bold}{green}Raspberry Pi{normal} selected")
    elif board_str == "t":
        spi, cs, reset = rpigs_tx_spi_config()
        rxtx_switch = RXTXSwitch(board.D26, board.D17, board.D27)
        radio = initialize_radio(spi, cs, reset, rxtx_switch=rxtx_switch)
        print(f"{bold}{green}RPiGS TX{normal} selected")
    elif board_str == "r":
        spi, cs, reset = rpigs_rx_spi_config()
        rxtx_switch = RXTXSwitch(board.D26, board.D17, board.D27)
        radio = initialize_radio(spi, cs, reset, rxtx_switch=rxtx_switch)
        print(f"{bold}{green}RPiGS RX{normal} selected")
    elif board_str == "c":
        tx_spi, tx_cs, tx_reset = rpigs_tx_spi_config()
        rx_spi, rx_cs, rx_reset = rpigs_rx_spi_config()
        rxtx_switch = RXTXSwitch(board.D26, board.D17, board.D27)
        radio = initialize_radio(tx_spi, tx_cs, tx_reset, rx_spi, rx_cs, rx_reset, rxtx_switch=rxtx_switch)
        print(f"{bold}{green}RPiGS TX and RX (dual radio){normal} selected")
    elif board_str == "o":
        spi, cs, reset = rpigs_spi_config()
        radio = initialize_radio(spi, cs, reset)
        print(f"{bold}{green}RPiGS TX and RX (single radio){normal} selected")
    else:
        raise ValueError(f"Board string {board_str} invalid")

    print_radio_configuration(radio)

    if get_input_discrete(
            f"Change radio parameters? {bold}(y/N){normal}", ["", "y", "n"]) == "y":
        manually_configure_radio(radio)
        print_radio_configuration(radio)

    return radio


def gs_shell_main_loop(radio):
    verbose = True
    while True:
        try:
            choice = get_input_discrete(f"\n{blue}Choose an action{normal}", flattend_prompt_options)
            if choice in prompt_options["Receive loop"]:
                print("Entering receive loop. CTRL-C to exit")
                while True:
                    tasko.add_task(read_loop(radio, debug=verbose), 1)
                    tasko.run()

            elif choice in prompt_options["Beacon request loop"]:
                beacon_period = get_input_range("Request period (seconds)", (10, 1000), allow_default=False)
                beacon_frequency_hz = 1.0 / float(beacon_period)
                logname = input("log file name (empty to not log) = ")
                def get_beacon_noargs(): return get_beacon(radio, debug=verbose, logname=logname)
                tasko.schedule(beacon_frequency_hz, get_beacon_noargs, 10)
                tasko.run()

            elif choice in prompt_options["Image request loop"]:
                image_period = get_input_range("Request period (seconds)", (120, 1000), allow_default=False)
                image_frequency_hz = 1.0 / float(image_period)
                def get_image_noargs(): return get_image(radio, debug=verbose)
                tasko.schedule(image_frequency_hz, get_image_noargs, 10)
                tasko.run()

            elif choice in prompt_options["Upload file"]:
                source = input('source path = ')
                dest = input('destination path = ')
                tasko.add_task(upload_file(radio, source, dest, debug=verbose), 1)
                tasko.run()
                tasko.reset()

            elif choice in prompt_options["Request file"]:
                source = input('source path = ')
                tasko.add_task(request_file(radio, source, debug=verbose), 1)
                tasko.run()
                tasko.reset()

            elif choice in prompt_options["Send command"]:
                command_name = get_input_discrete("Select a command", list(commands_by_name.keys())).upper()
                command_bytes = commands_by_name[command_name]["bytes"]
                will_respond = commands_by_name[command_name]["will_respond"]
                args = input('arguments = ')

                tasko.add_task(send_command_task(radio, command_bytes, args, will_respond, debug=verbose), 1)
                tasko.run()
                tasko.reset()

            elif choice in prompt_options["Set time"]:
                while True:
                    t = input("seconds since epoch (empty for system time) = ")
                    if t == "":
                        t = None
                        break
                    else:
                        try:
                            t = int(t)
                            break
                        except ValueError:
                            print("Invalid time - must be empty or an integer")

                tasko.add_task(set_time(radio, t, debug=verbose), 1)
                tasko.run()
                tasko.reset()
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

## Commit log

2023-10-19 Satellite content added
    [+Y Rail.step, -Y Rail.step, 1040310811.stp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]
2023-11-10 General HW update
    [BOM_avionics-batteryboard-bottom_EUROCIRCUIT.xlsx, BOM_avionics-batteryboard-bottom_JLCPCB.xlsx, BOM_avionics-batteryboard-bottom_PCBWAY.xlsx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]
2023-11-10 update HW
    [BusProtection.kicad_sch, Solar-Panel-X+.kicad_pcb, Solar-Panel-X+.kicad_sch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]
2023-11-10 update BOM
    [Bus Protection.kicad_sch, BusProtection.kicad_sch, Solar-Panel-X+.kicad_sch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]
2023-11-18 Updated I2C address resistors; Added reference to KiCad docs
    [Solar-Panel-X+.kicad_sch, Solar-Panel-X-.kicad_sch, Solar-Panel-Y+.kicad_sch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]
2024-01-04 Revision B3/03 boards added
    [BusProtection.kicad_sch, Solar-Panel-X.kicad_pcb, Solar-Panel-X.kicad_sch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]
2024-01-14 RPi ground station board files added
    [Radio HAT.kicad_pcb, Radio HAT.kicad_sch]
2024-02-04 Battery boards rev B3/03 added
    [Bus Protection.kicad_sch, Radio HAT.kicad_pcb, batteryboard-bottom.kicad_pcb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]
2024-04-05 RPi ground station updated
    [RPi GS hat board.kicad_pcb, RPi GS hat board.kicad_sch, Radio HAT.kicad_pcb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]
2024-04-10 general update
    [Bus Protection.kicad_sch, BusProtection.kicad_sch, GS_RPi_BOM.xlsx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]
2024-06-19 RPiGS updated files
    [Radio HAT.kicad_pcb, Radio HAT.kicad_sch]
2025-03-19 Minor fix in image compiling
    [gs_commands.py]
2025-03-19 Clarified ground station instructions
    [RPi GS hat board.kicad_pcb, RPi GS hat board.kicad_sch]

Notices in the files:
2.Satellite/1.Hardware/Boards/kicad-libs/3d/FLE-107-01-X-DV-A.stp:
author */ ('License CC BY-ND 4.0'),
